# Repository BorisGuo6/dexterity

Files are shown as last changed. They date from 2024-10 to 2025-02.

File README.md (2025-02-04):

# Project Dexterity

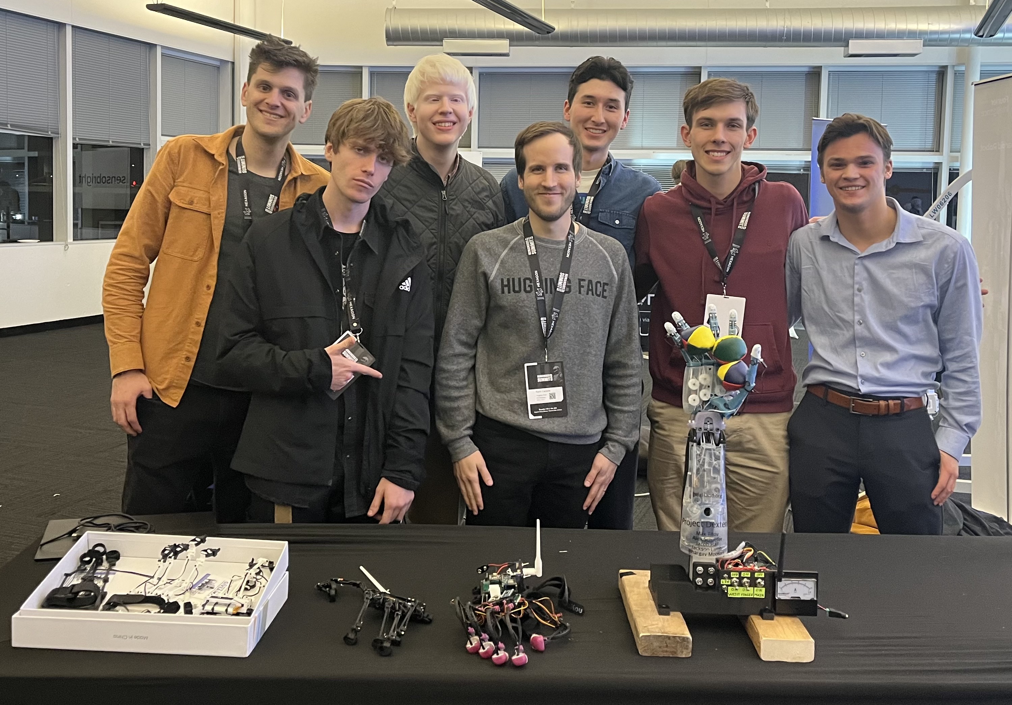
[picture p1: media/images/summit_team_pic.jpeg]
Team Pic at Humanoids Summmit


## Overview
Dexterity is a capstone project developed by ECE students at the University of Virginia (Class of 2025). The project consists of a robotic hand that can be controlled using a haptic feedback glove, providing a natural and intuitive way to control robotic movements while receiving tactile feedback. Three members of our team traveled to the Bay Area in December 2024 to showcase the project at the [Humanoids Summit](https://humanoidssummit.com/) in the Hugging Face booth (pictured above).

An summary of the project can be found in these [Figma slides](https://www.figma.com/deck/h1ZrgHnDu9oTQfUKUapgQW/Dexterity-Progress-Report?node-id=32-46&t=BGETurAAA480CFCk-1).

## Videos

The videos below showcase how the system's responsiveness and precision enable it to consistently catch balls.

https://github.com/user-attachments/assets/b5050c01-b495-40dd-bd65-899a9acaca80

https://github.com/user-attachments/assets/4d67e1bd-996e-49d0-b71a-232bf0a58b3a

## Project Structure
### [Firmware](firmware/)
- `HapticGlove/` - Firmware for the V2 control glove
- `RoboticArm/` - Firmware for the dexhand
- `PrototypeGlove/` - Firmware for the prototype control glove 
- `ESPNOW/` - ESP-NOW wireless communication implementations
- `test/` - Various test implementations and debugging tools

### [Hardware](hardware/)
- `cad/` - CAD files for 3D printing
  - `arm base/` - CAD files for the arm base and wire organization
  - `glove v2.4/` - CAD files for the latest interation of the V2 glove
  - `old/` - CAD files for the previous iterations of the V2 glove
- `pcb/`
  - `Forearm/` - PCB design files for the forearm
  - `Hand/` - PCB design files for the hand
  - `Library/` - KiCad library files
  - `gerber/` - Gerber files for manufacturing

### [Capstone](capstone/)
- `requirements/` - Project requirements and specifications from our capstone class 
- `reports/` - Project reports and presentations from our capstone class 

### [Media](media/)
- `images/` - Photos of the project and components
- `videos/` - Demo videos and presentations
- `diagrams/` - System diagrams and illustrations

## Features

### Robotic Arm
- Based on the open-source [Dexhand](https://www.dexhand.org/) project
  - Forearm shell and arm base were FDM printed using PETG filament
  - Everything else was resin printed using ABS-like resin, which provided smoother finishes and more accurate fits due to the higher resolution of SLA printing
- 16 degrees of freedom (DOF) across five fingers
  - 3 DOF per finger (flexion of PIP, flexion of MCP, abduction/adduction)
  - 4 DOF for thumb (extra degree for rotation)
  - Controlled by EMAX ES3352 digital servos
- 2 DOF in the wrist (pitch and yaw)
  - Controlled by Feetech SCS2332 serial servos 
  - These provide increased range of motion and torque in addition to having overcurrent protection
- Controlled by ESP32-S3 DevKitC-1 microcontroller
  - Housed on a Proto-PCB
  - ESP-NOW protocol for low-latency communication
- Force-sensitive resistors on each fingertip
  - 5kg maximum pressure sensing
  - These are wired up to a voltage divider circuit that connects to ADC channels on the ESP32
- System is powered by a 6V 10A power supply
  - Directly supplies power to servos
  - 3.3V regulation for control electronics
  - Wired through an amp meter for monitoring current draw

<p float="left">
  
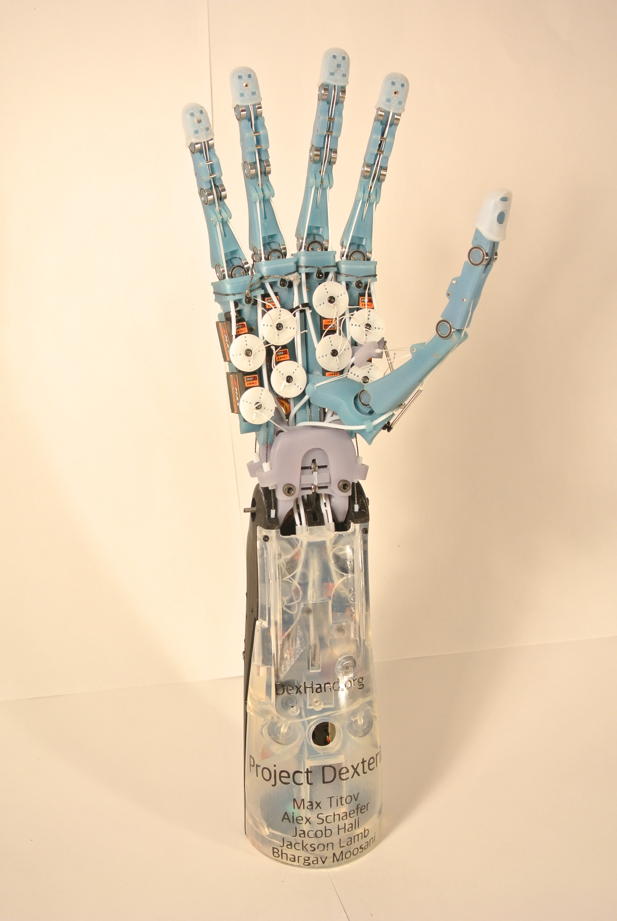
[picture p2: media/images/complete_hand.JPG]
   
</p>

### Prototype Glove
- Original repository can be found here: [Prototype Finger Tracker](https://github.com/max-titov/finger-tracker)
- Hall effect sensor-based finger tracking
  - Each joint that was tracked had a rotating magnet and a hall effect sensor
  - 3 DOF per finger (flexion of PIP, flexion of MCP, abduction/adduction)
  - 4 DOF for thumb (extra degree for rotation)
  - Multiplexed sensor reading
- Controlled by a Xiao ESP32-C3 microcontroller
  - ESP-NOW protocol for low-latency communication
- Provided very accurate and responsive finger tracking

<p float="left">
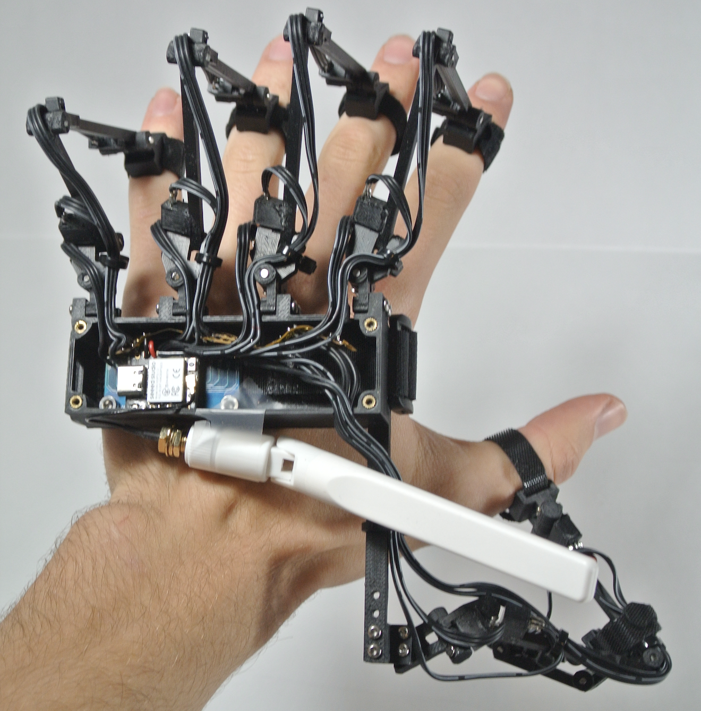
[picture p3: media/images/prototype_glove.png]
  
</p>

### V2 Control Glove
- Same hall effect sensor-based finger tracking as the prototype glove
  - 16 sensors total
  - Electrical complexity of the system introduced a lot of noise into the system, making the finger tracking less accurate than the prototype glove
- Dual PCB design
  - Hand PCB for sensors and haptics
  - Forearm PCB for processing and power
  - Connected with two ribbon cables
- Dual IMU system for wrist orientation
  - One IMU on hand PCB
  - One IMU on forearm PCB
  - Quaternion-based orientation calculation
- Haptic feedback system
  - Linear Resonant Actuators on each fingertip
  - I2C multiplexer for managing multiple LRA drivers
  - Variable intensity based on pressure sensing
- 3D printed design
  - Finger buckets housed LRA drivers and clamped onto fingers using rubber bands
  - Modular finger assemblies allowed easy swapping of parts during development
  - 2 straps per PCB housing attached the device to your hand
- Controlled by ESP32-S3 DevKitC-1 microcontroller
  - Housed on the Forearm PCB
  - ESP-NOW protocol for low-latency communication
- Control panel with LED indicators and mode switches
- Capable of running on battery power due to the onboard 3.3V regulator

<p float="left">
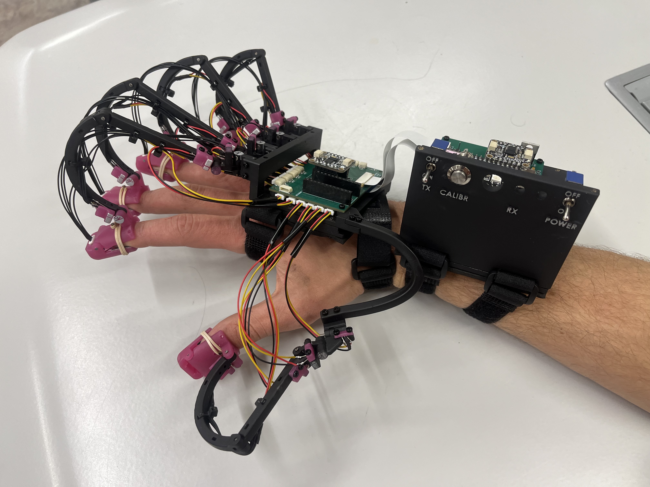
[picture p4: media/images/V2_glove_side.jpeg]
  
</p>

## Getting Started
1. Good luck with building everything :)
2. Clone the repository
3. Install PlatformIO extension for VSCode
4. Open the desired project folder
5. Build and upload to your device

## Authors

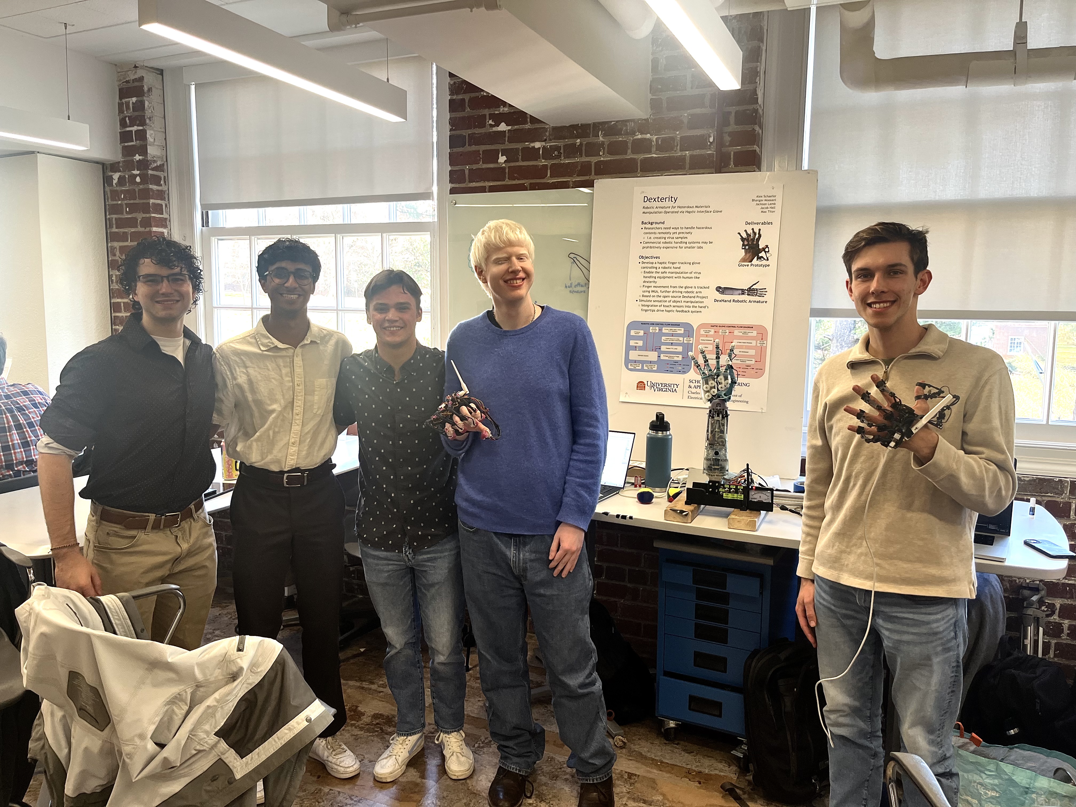
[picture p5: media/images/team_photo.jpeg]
Team Pic at UVA Demo Day


- Max Titov 
  - Led the team by doing high level design of the whole system, assembled the robotic arm, designed the control gloves, and developed finger tracking/control libraries
  -   
- Alex Schaefer 
  - Architected the embedded software system, implemented ESP-NOW communication, and developed the high-level control structure using multi-threading
  -  
- Jackson Lamb 
  - Designed and tested the dual PCB system for the control glove and developed libraries for the control panel interfaces
  -  
- Jacob Hall 
  - Implemented the dual IMU system for wrist tracking, including quaternion mathematics and calibration routines
  -  
- Bhargav Moosani 
  - Designed and implemented the haptic feedback system using LRAs and force sensors, including wireless integration
  -  

## Acknowledgments
- [Original Dexhand Repository](https://github.com/TheRobotStudio/V1.0-Dexhand/) - Our robotic hand design is based on The Robot Studio's Dexhand project, licensed under CC BY-NC-SA 4.0.
- [Dexhand Website](https://www.dexhand.org/) - Trent Shumay from IoT Design Shop built two Dexhands and put together a website that compiled info about the project into a single page.
- [Prototype Finger Tracker](https://github.com/max-titov/finger-tracker) - My first glove that tracked 16 DOF of the fingers. This glove was used in a lot of the demonstrations of the teleop due to its better finger tracking capabilities.
- [Nepyope's Youtube](https://www.youtube.com/watch?v=iPtgvh6fNdQ) - The video of the first 16 DOF glove using hall effect sensors that inspired this whole project.
- [Nepyope's Project Homunculus](https://github.com/nepyope/Project-Homunculus) - The repository for the glove that inspired this project.

## License
This project is licensed under the MIT License - see the LICENSE file for details

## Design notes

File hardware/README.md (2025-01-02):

# Hardware

This directory contains the hardware design files for the project, organized into three main sections:

## BOM (Bill of Materials)
The Project Dexterity BOM excel spreadsheet (also available as a [google sheet](https://docs.google.com/spreadsheets/d/1TfbwuFHU-D9O60yxQ3oRrJCOd3qs4ftfMmc7sZDtarE/edit?usp=sharing)) contains part lists organized into 3 sheets: 
- Robotic Arm BOM
- Control Glove BOM
- General BOM

## CAD (Computer-Aided Design)
The CAD directory contains 3D models and mechanical design files for the physical components of the project. The models were designed in SolidWorks and are avaiable as SLDPRT files. Each folder contains a folder with all the STLs as well.
- `arm base/` - CAD files for the arm base and wire organization
- `glove v2.4/` - CAD files for the latest interation of the V2 glove
- `old/` - CAD files for the previous iterations of the V2 glove

## PCB (Printed Circuit Board)
The PCB directory contains the electronic design files for the circuit boards. These include:
- `Forearm/` - PCB design files for the forearm
- `Hand/` - PCB design files for the hand
- `Library/` - KiCad library files
- `gerber/` - Gerber files for manufacturing

We ordered the PCBs from [JLCPCB](https://jlcpcb.com/). Pictures of the PCBs are below:

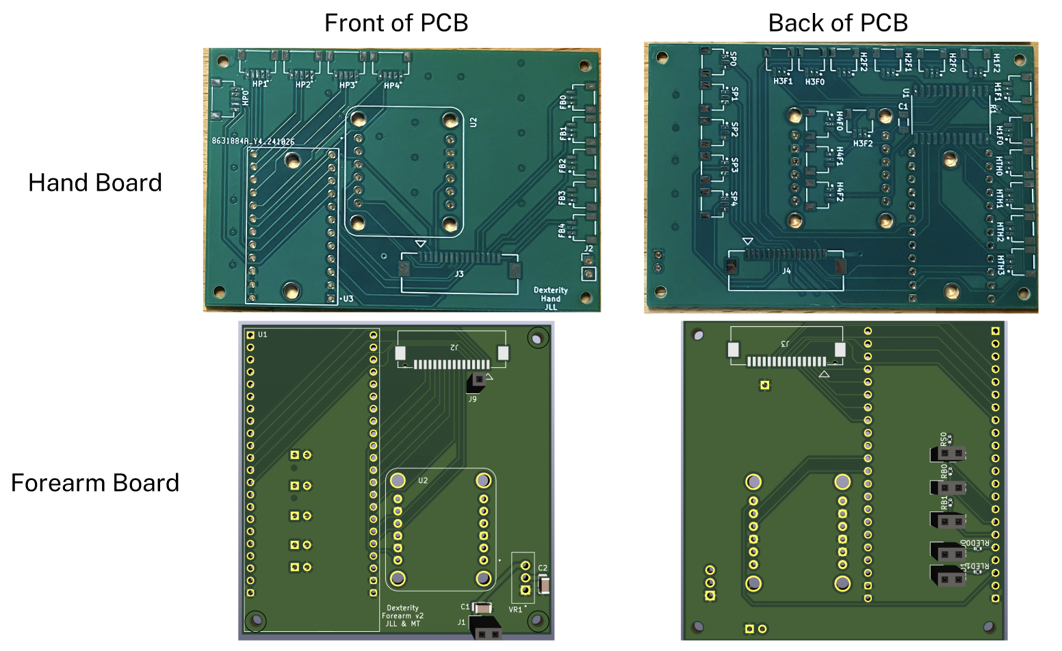
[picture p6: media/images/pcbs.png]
PCBs


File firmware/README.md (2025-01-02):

# Firmware

The Dexterity system consists of a haptic control glove and robotic arm that work together to enable remote manipulation of objects. The system uses ESP-NOW wireless communication to transmit position and force feedback data between the glove and arm with low latency.

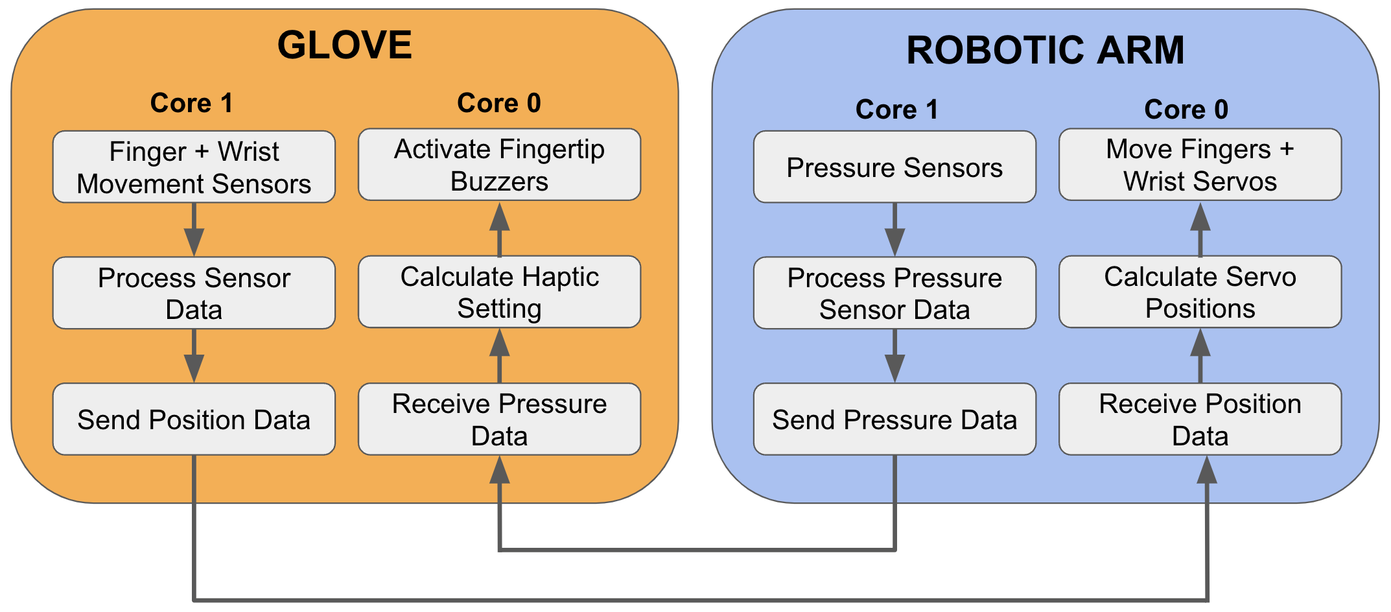
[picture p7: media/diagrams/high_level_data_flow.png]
High Level Data Flow Diagram


## System Architecture

The ESP32's dual-core architecture enables parallel processing of haptic feedback and position control. Core 1 handles initialization, with FreeRTOS managing resource allocation across both cores. The pressure sensor-to-LRA feedback pipeline runs on one core, while position sensing-to-servo control runs on the other. Timer-based ISRs ensure 50 Hz processing rates for both pipelines. The system uses ESP-NOW for wireless communication, with pressure data categorized into five intensity levels for haptic feedback, and position data from Hall Effect sensors and IMUs controlling servo movements.

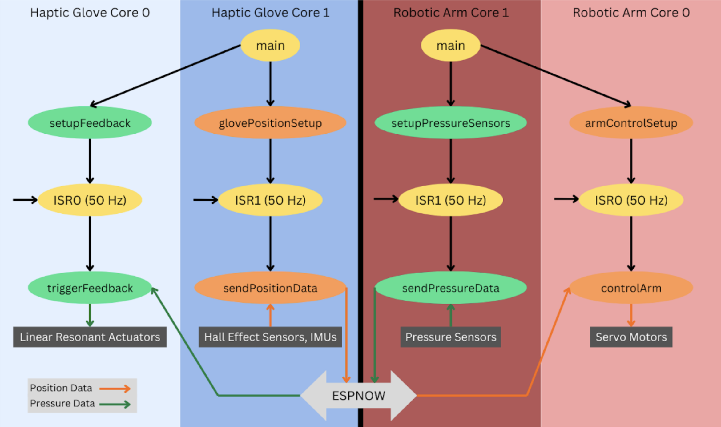
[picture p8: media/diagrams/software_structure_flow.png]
Software Data Flow Diagram


## HapticGlove
Firmware for the V2 control glove. The glove uses hall-effect sensors and IMUs to track finger and wrist movements, which are processed and sent wirelessly to control the robotic arm. It receives pressure sensor data from the arm and provides haptic feedback through LRA vibration motors on the fingertips. Descriptions of each library can be found here: [HapticGlove Libraries](HapticGlove/lib/)

## RoboticArm 
Firmware for the robotic hand. The arm receives position commands from the glove and moves its servos to match the user's movements. It uses pressure sensors to detect contact forces and sends this data back to drive the glove's haptic feedback. Descriptions of each library can be found here: [RoboticArm Libraries](RoboticArm/lib/)

## PrototypeGlove
Firmware for the initial prototype control glove used for testing and development. Descriptions of each library can be found here: [PrototypeGlove Libraries](PrototypeGlove/lib/)

## ESPNOW
Example implementations and testing code for ESP-NOW wireless communication between devices.

## test
Various test implementations and debugging tools for development and validation.

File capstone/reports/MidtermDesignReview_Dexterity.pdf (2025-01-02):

## Dexterity - Midterm Design Review

Alex Schaefer
Bhargav Moosani
Jackson Lamb
Jacob Hall
Max Titov

## Dexterity: Overview

Background

- Researchers handle hazardous contents in labs frequently → risky predicament
- i.e. preparing virus samples or handling poisonous substances
- Robotic handling systems are expensive
- Barriers of entry for smaller labs

Objectives

- Provide researchers and labs with a safe, cost-effective approach to hazardous material manipulation, which can be used for their lab-specific needs

## Dexterity: Deliverables

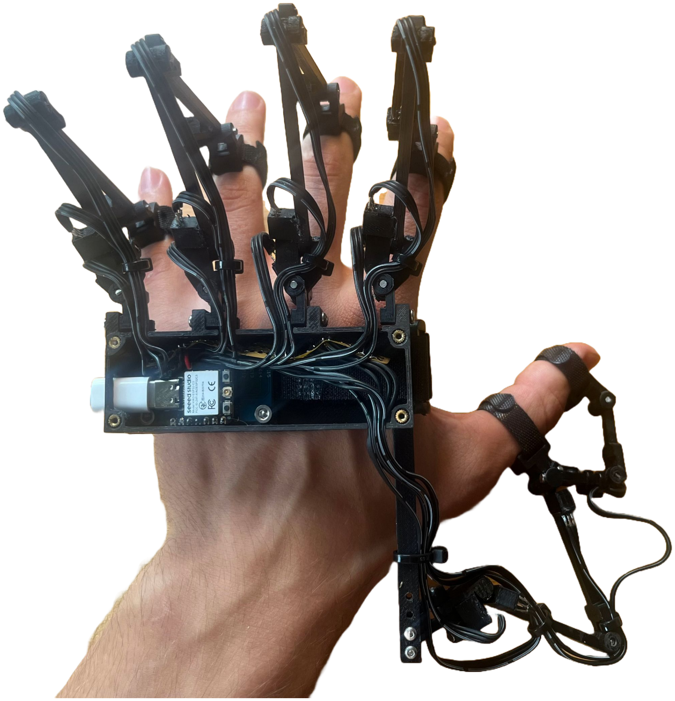
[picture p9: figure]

Control Glove Prototype

Control Glove

- Hall effect sensors and IMUs track hand motion to drive the robotic armature
- Linear actuators provide haptic pulses for touch feedback from the robotic arm

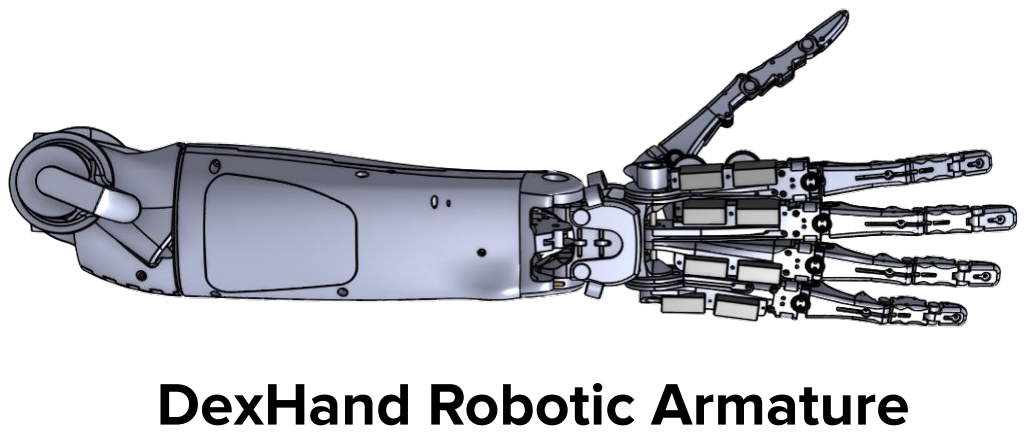
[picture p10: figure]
DexHand Robotic Armature

Robotic Armature

- CAD based off the open-source Dexhand project
- Pressure sensors on each fingertip to drive linear actuators on control glove

# Design

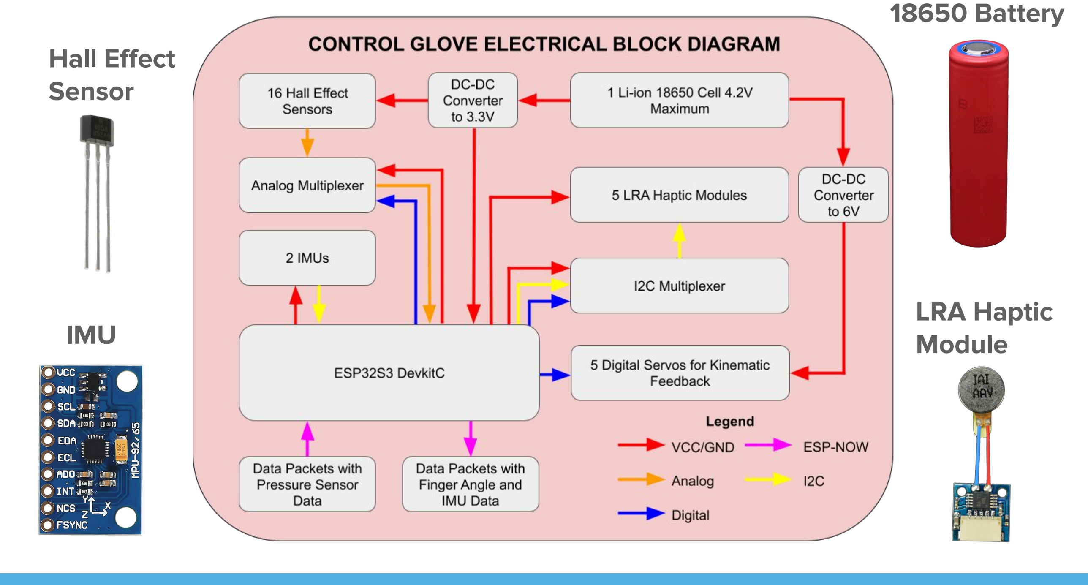
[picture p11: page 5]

Hall Effect
Sensor

IMU

LRA Haptic
Module

18650 Battery

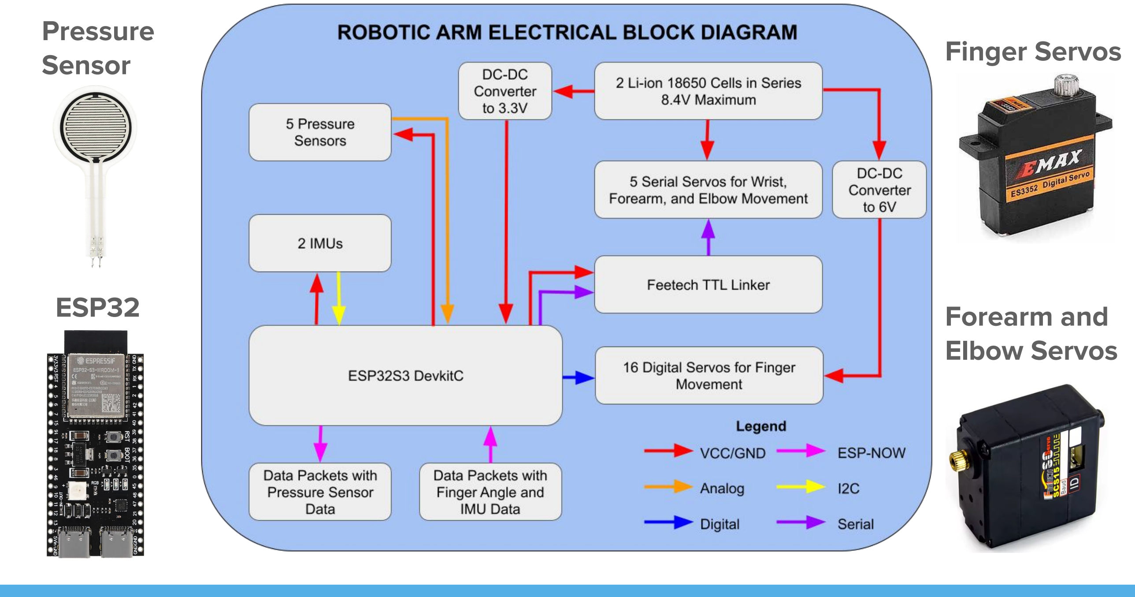
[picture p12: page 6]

Pressure
Sensor

ESP32

Finger Servos

Forearm and
Elbow Servos

## Glove Sensor Processing Software Flowchart

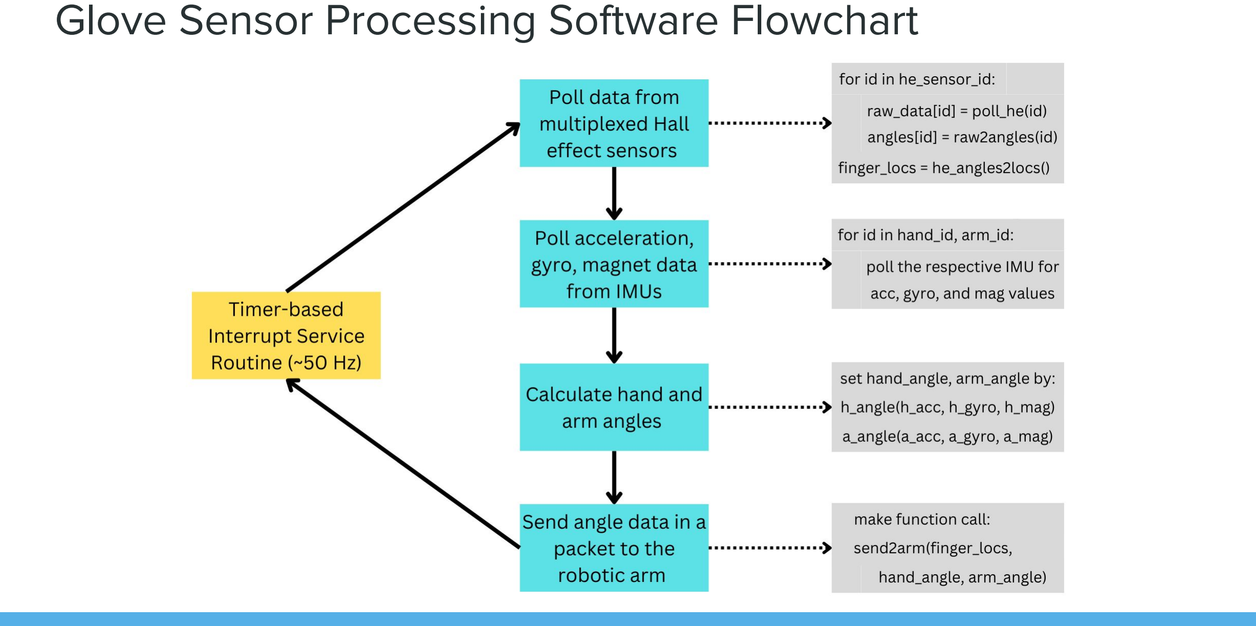
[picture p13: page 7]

## Glove Haptic Data Processing + Control Software

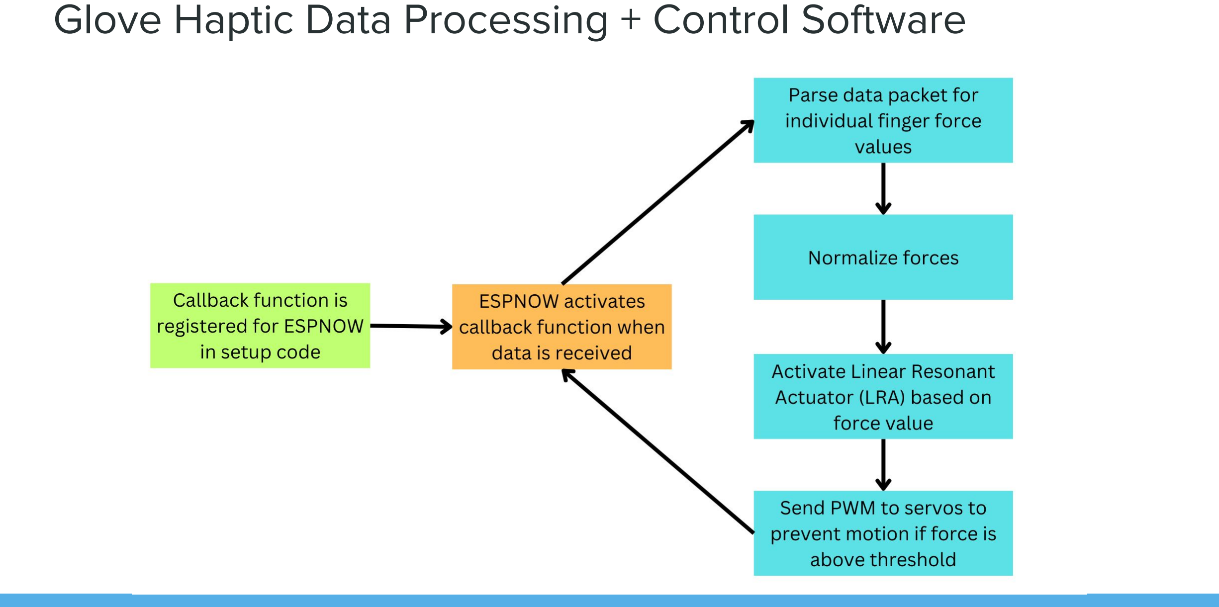
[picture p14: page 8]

ESPNOW Wireless Communication Protocol

Callback Function ran every time a packet from robotic arm is received

- Packet parsed into individual finger forces (from touch sensors)
- Forces are normalized
- Normalized forces are used to activite LRAs (Linear Resonant Actuator)
- (Optional) Servo Motors on Glove actuated to prevent motion

## Robotic Arm Software

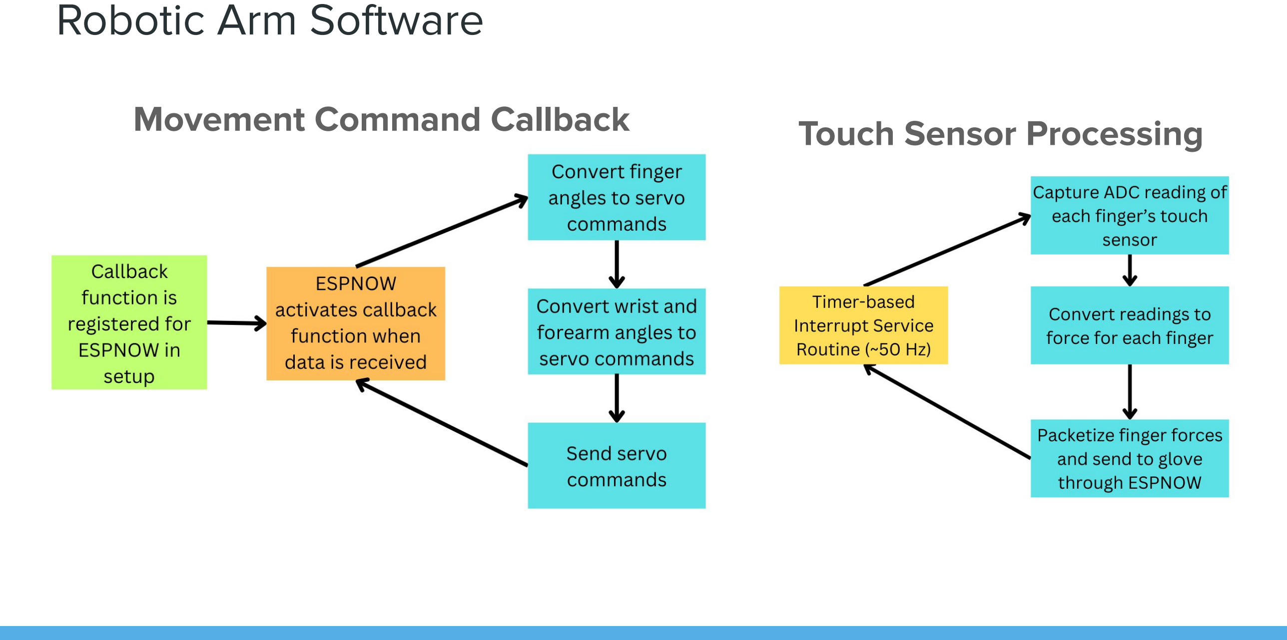
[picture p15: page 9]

Movement Command Callback | Touch Sensor Processing

## Control

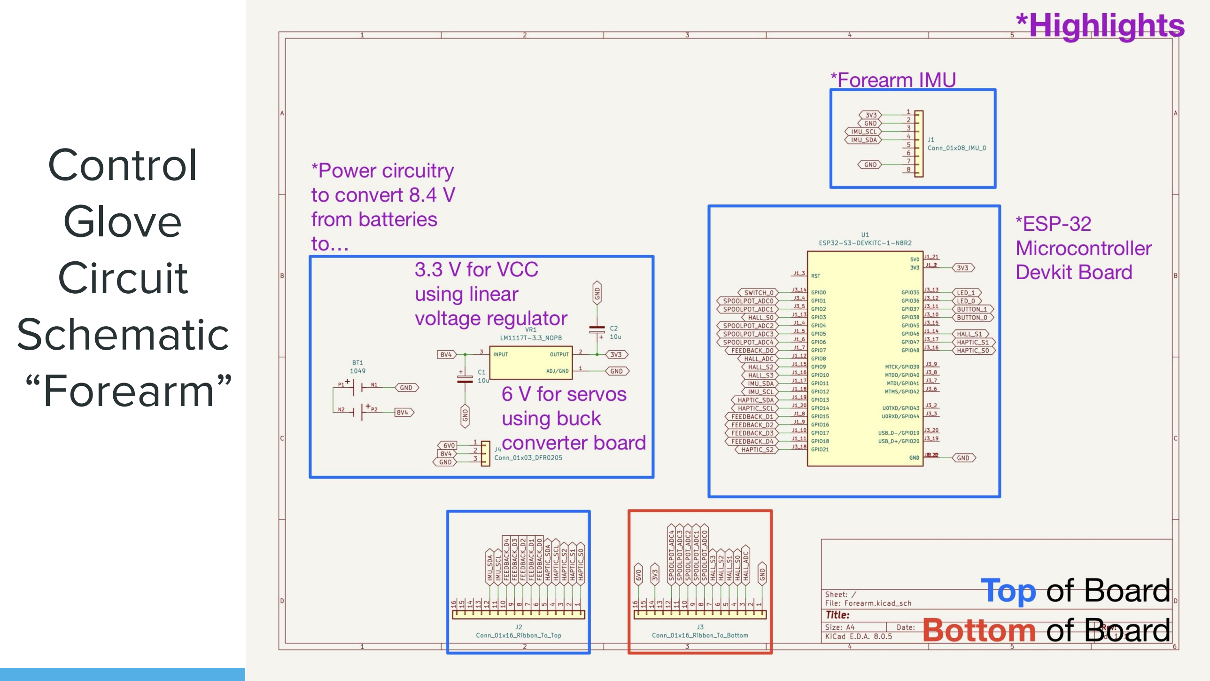
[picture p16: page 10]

## Glove Circuit Schematic “Forearm”

## Control

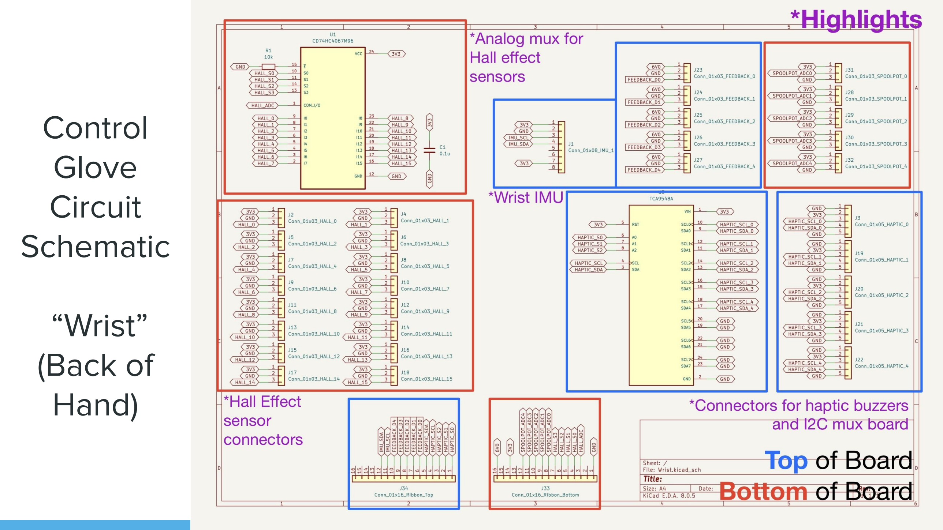
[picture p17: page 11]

## Glove Circuit Schematic

## “Wrist” (Back of Hand)

# Test Plan

## Robotic Arm Testing

After assembling the finger and thumb assemblies:

- Test 3 Degrees of Freedom (DOF) for each finger to ensure each joint can move independently and with the correct range of motion.
- Test 4 DOF for the thumb to confirm full movement, including opposability.

After assembling the wrist and forearm:

- Test 2 Degrees of Freedom for wrist
- Test 2 Degrees of Freedom for forearm

## Control Glove Testing

### 1. Hall Effect Sensor

- Test the 16 hall effect sensors on a breadboard to ensure they are reading magnetic field changes accurately

### 2. Finger Linkage Assembly

- Test that the 16 hall effect sensors still work after assembly, ensuring no mechanical interference

### 3. IMU Accuracy

- Test both IMUs to verify that they provide accurate orientation data post-assembly

### 4. Communication

- Test sending and receiving packets between ESP32 microcontrollers to verify reliable wireless data exchange

## Complete System Testing

### 1. Communication

- Test that packets are successfully sent and received between both ESP32 microcontrollers in complete system

### 2. Control

- Test controlling 1 finger with the control glove
- Test controlling all 5 fingers with the control glove
- Test controlling wrist movement using IMU data
- Test controlling forearm and elbow movement using IMU data

### 3. Haptic Feedback

- Test the haptic response of all 5 fingers to confirm uniform and reliable feedback across all fingers

### 4. Calibration

- Test the calibration of the control glove to the robotic arm to ensure that hand movements and forces are accurately translated to the robotic system

# Timeline

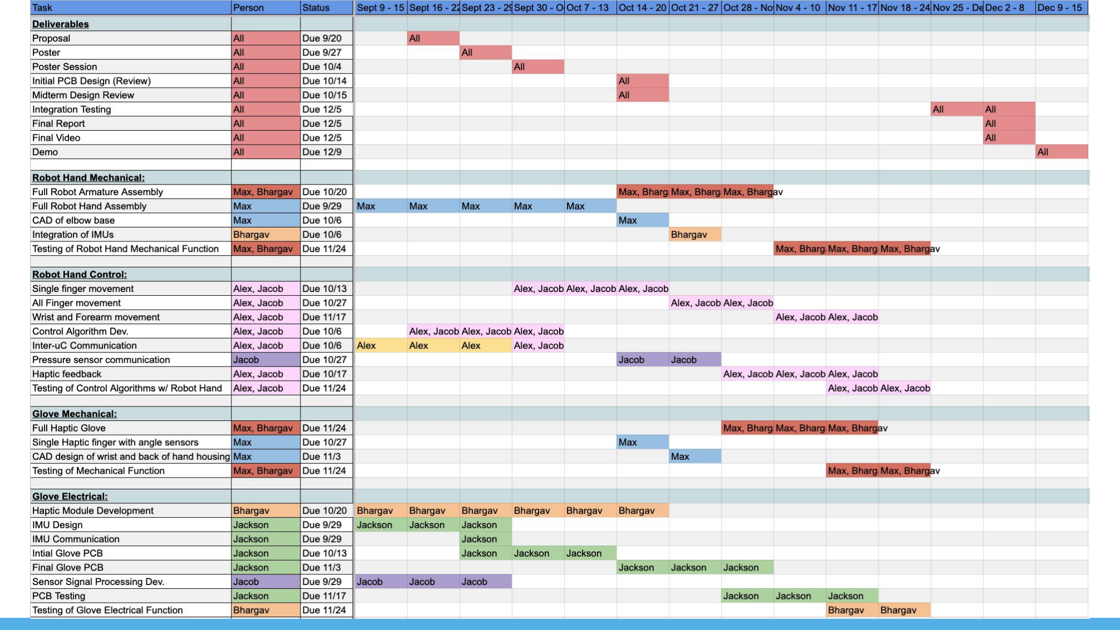
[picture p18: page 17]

# Questions?

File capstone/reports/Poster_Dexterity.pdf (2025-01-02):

# Dexterity

### Background

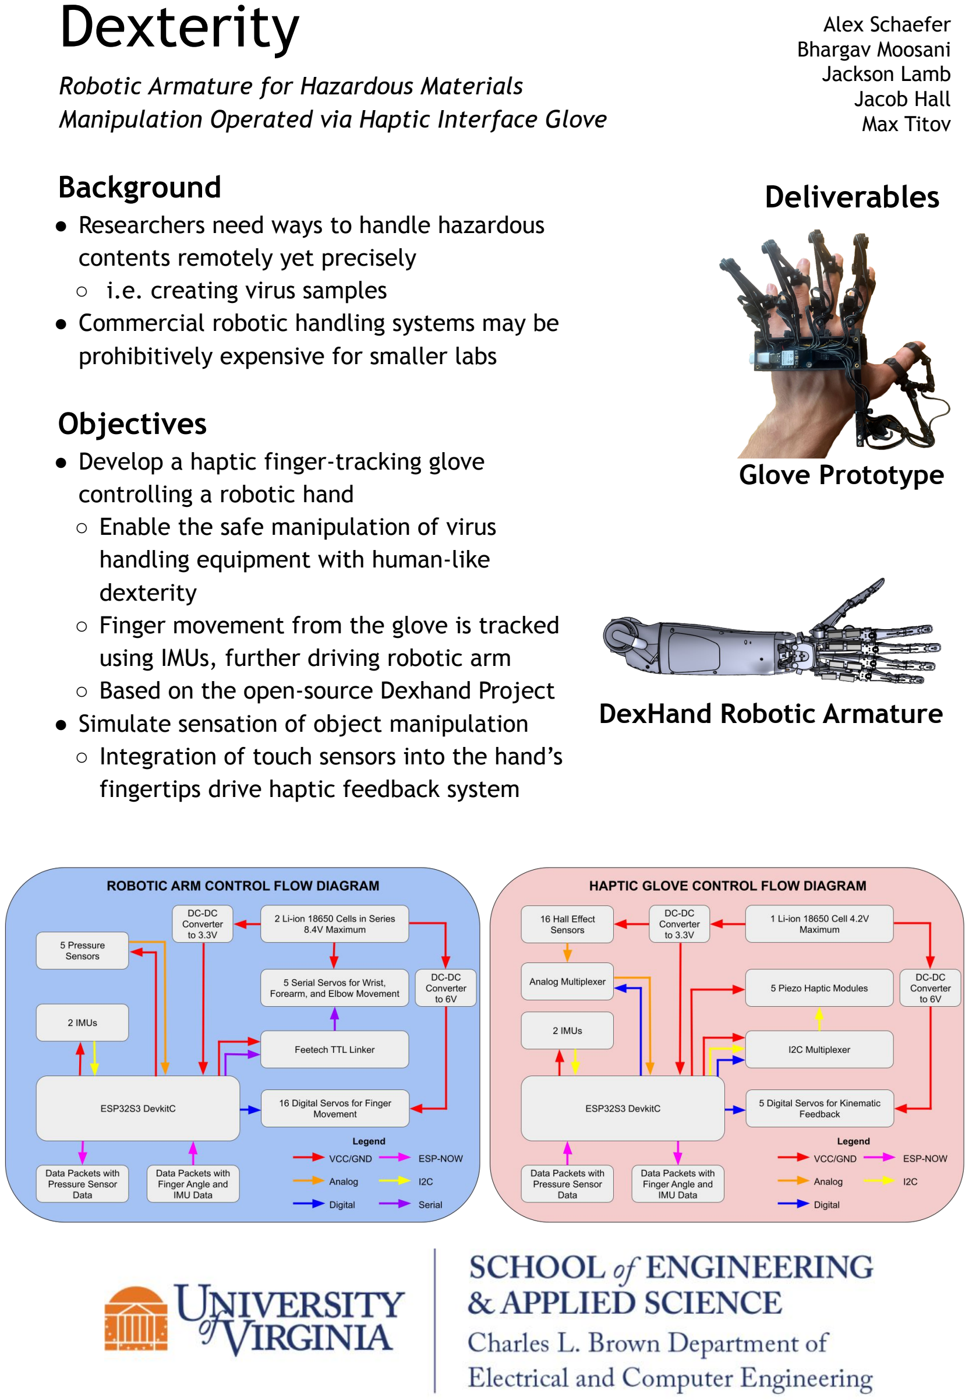
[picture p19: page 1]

Robotic Armature for Hazardous Materials Manipulation Operated via Haptic Interface Glove

- Researchers need ways to handle hazardous contents remotely yet precisely
- i.e. creating virus samples
- Commercial robotic handling systems may be prohibitively expensive for smaller labs

### Objectives

- Develop a haptic finger-tracking glove controlling a robotic hand
- Enable the safe manipulation of virus handling equipment with human-like dexterity
- Finger movement from the glove is tracked using IMUs, further driving robotic arm
- Based on the open-source Dexhand Project
- Simulate sensation of object manipulation
- Integration of touch sensors into the hand’s fingertips drive haptic feedback system

Alex Schaefer
Bhargav Moosani
Jackson Lamb
Jacob Hall
Max Titov

Glove Prototype

DexHand Robotic Armature

### Deliverables

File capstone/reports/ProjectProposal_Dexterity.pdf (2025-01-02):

# Dexterity

Robotic Armature for Hazardous Materials Manipulation Operated via Haptic Interface Glove Alex Schaefer, Bhargav Moosani, Jackson Lamb, Jacob Hall, Max Titov

Abstract

This project aims to develop a haptic finger-tracking glove that controls a robotic hand, enabling safe manipulation of hazardous materials while maintaining human-like dexterity. The system consists of a glove that tracks the user’s finger movement, coupled with inertial measurement units (IMUs) to monitor hand and forearm orientation. This motion-tracking system drives a robotic arm based on the open-source Dexhand project. We will integrate touch sensors on each robotic fingertip that activate the glove's electromagnetic brake system. These brakes create tactile feedback by restricting finger movement, simulating the sensation of object manipulation. This haptic feedback, combined with the precise motion tracking, allows for intuitive and accurate control of the robotic hand in hazardous environments.

Background

The increasing need for safe and cost-effective solutions in laboratories handling hazardous materials has driven our team to develop a haptic finger and forearm-tracking glove system that controls a robotic hand. This system is designed to enable researchers to interact with toxic substances while maintaining human-like dexterity and without the need for expensive fume hoods or overly complex robotic setups. The core innovation of our project lies in creating a much more affordable and user-friendly alternative compared to existing commercial solutions, making this technology accessible to a wider audience of researchers and laboratories.

Prior Work

Commercial products such as HaptX [1], (https://www.zotero.org/google-docs/?hcelSB) SenseGlove [2], (https://www.zotero.org/google-docs/?vWltXo) and Weart [3] (https://www.zotero.org/google-docs/?kayynv) have set the standard in the haptic feedback and remote manipulation market, offering highly immersive and precise systems. These technologies allow users to interact with virtual environments or robotic systems while experiencing realistic tactile feedback. However, these products are often prohibitively expensive and primarily serve industrial applications, limiting their accessibility to smaller research labs and educational institutions.

In the open-source space, projects like LucasVR [4] (https://www.zotero.org/google-docs/?fwQZJJ) and Nepyope's VR Glove [5] (https://www.zotero.org/google-docs/?h1ueZ5) have demonstrated innovative solutions for hand-tracking and haptic feedback. These projects offer promising foundations, especially in terms of making the technology more accessible. However, they lack the focus on safe, real-world interaction with hazardous materials, as their primary use cases lie within virtual reality environments.

Our project differentiates itself in two key ways: cost and target audience. By leveraging open-source designs and affordable components, we aim to drastically reduce the overall cost of the system, making it viable for smaller research institutions and universities. Our system also targets laboratories that require safe manipulation of hazardous materials. Unlike existing virtual reality or industrial solutions, our glove allows researchers to remotely control a robotic hand to handle toxic substances with haptic feedback, improving both safety and ease of use without the need for costly equipment or infrastructure.

Coursework Preparation

Our coursework at the University of Virginia has provided a strong foundation for this project. Several key courses have directly prepared us for the technical challenges involved:

- Intro to Embedded Computing Systems has given us a solid understanding of microcontrollers and real-time systems, both critical for the responsive control of the glove and robotic arm.
- Electromagnetic Fields helped us understand the fundamentals of how electromagnetic braking systems can be implemented to simulate tactile feedback in the glove.
- Intro to Control Systems and Signals & Systems laid the groundwork for developing the precise control algorithms necessary for converting user hand movements into corresponding robotic arm movements.
- Electronics provided us with the skills to design and integrate the necessary hardware components, such as sensors and actuators, into a compact and efficient system.
- Computer-Aided Design has allowed us to design and/or modify existing models of both the glove and robotic arm components in a way that is both ergonomic and easy to manufacture, ensuring that the final product is as user-friendly as it is functional.

By applying the principles and techniques we have learned in these courses, we are well-equipped to develop a system that not only tracks hand movements accurately but also provides real-time, tactile feedback to the user. This combination of coursework and innovative design will allow us to bring a cost-effective, high-functioning tool to laboratories where safety and precision are paramount.

Description of Project

How it Works/Technical Details

Overview
As can be seen in Figure 1 below, the Dexterity system consists of a user-worn glove consisting of a suite of sensors with a haptic interface and a robotic arm controlled by the glove. At a high level, there sensor signals from each of the fingers and the forearm are processed into movement commands sent to the robotic arm. Upon receiving these commands, the robotic arm fingers and forearm are manipulated to match that of the glove as close as possible. The robotic arm has a suite of touch sensors, whose data is processed into haptic commands sent back to the glove. The glove processes these haptic commands and restricts movement of the user’s fingers.

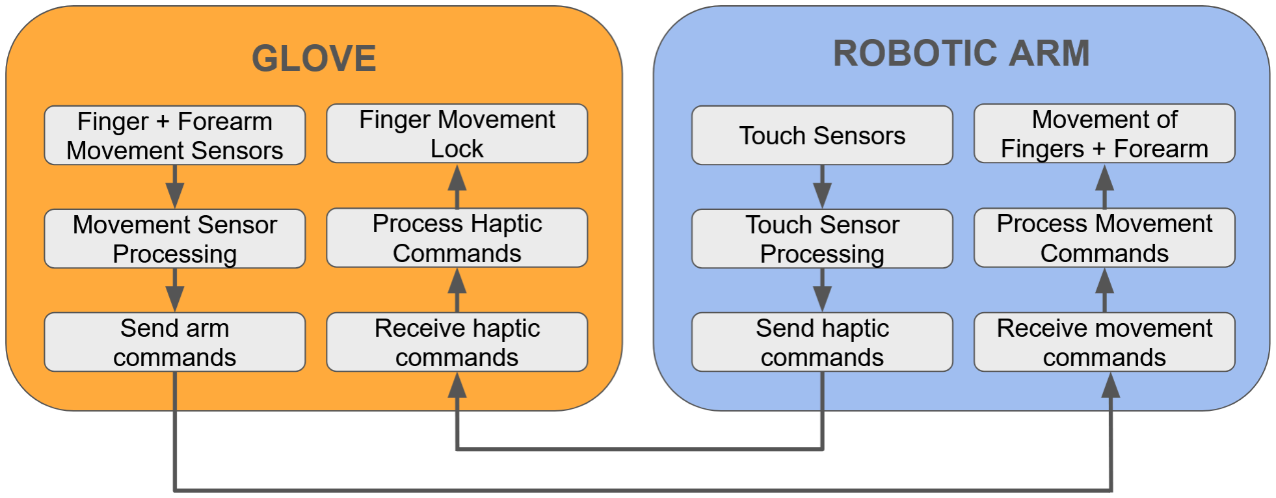
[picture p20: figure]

Figure 1: Complete System-Level Diagram

Robotic Arm
Our robotic arm is based on the open source project called the Dexhand [6]. (https://www.zotero.org/google-docs/?zinsQ2) The arm, up to the elbow, has 19 degrees of freedom that are controlled by servo motors. The fingers will account for 16 of these: 3 per finger and 4 for the thumb. The wrist has 2 degrees of freedom, and the rotation of the forearm accounts for the last degree of freedom. One modification we are making to the design is adding an elbow base with 2 degrees of freedom. This base will be securely attached to a table or rolling cart to provide stability to the rest of the hand. With our modifications, the hand will have a total of 21 degrees of freedom. An overview of the CAD can be seen in Figure 2.

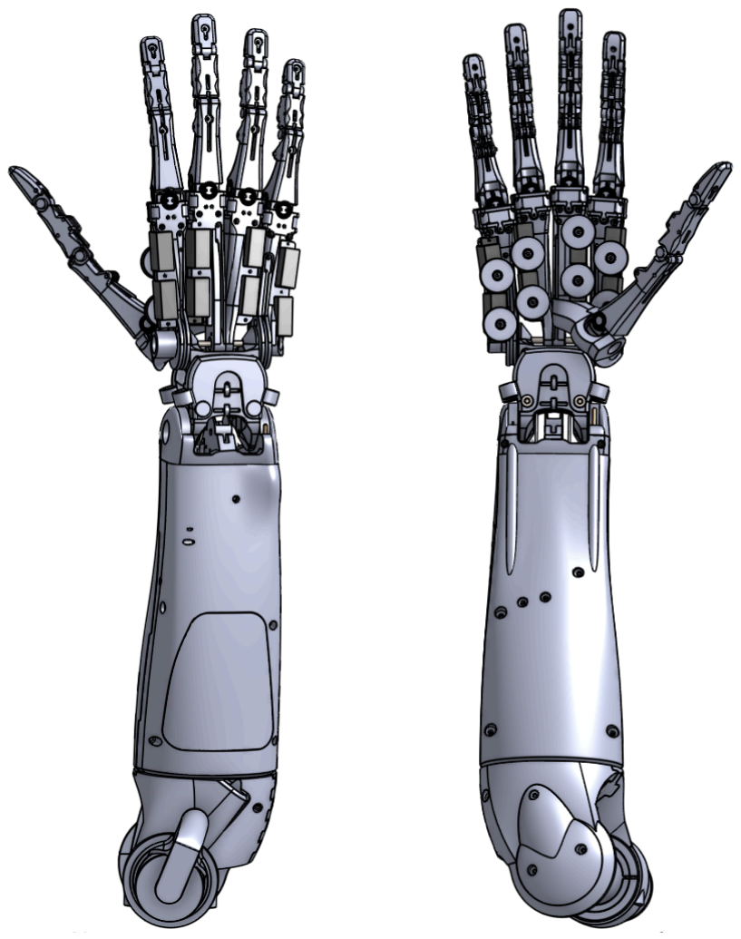
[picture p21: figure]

Figure 2: CAD Model of Robotic Arm

Another key modification that we are making to the original design is the integration of pressure sensors in each fingertip. These readings from the pressure sensors will be transmitted to the control glove to engage haptic feedback to create the sensation of holding an object in the user. Additionally we are adding two IMUs: one on the back of the robot hand and one on the back of the forearm. These sensors will be in the same locations on the control glove. To create wrist, forearm, and elbow movement, the robot hand will try to match its IMUs readings to the control gloves IMU readings by moving the wrist and forearm in the appropriate direction. This will be accomplished using PID (proportional integral derivative) [7] (https://www.zotero.org/google-docs/?FtU3I5) loops to control the servos.

This robotic arm control system is built around an ESP32S3 DevkitC microcontroller. It's powered by two Li-ion cells and uses DC-DC converters to regulate 6V for the digital servos and 3.3V for the ESP32. The control glove sends ESP-NOW [8] (https://www.zotero.org/google-docs/?ZmDn0H) data packets containing IMU and finger angle data. After processing this data, the ESP32 sends digital signals to control the 16 finger servos and serial data to control the 5 serial servos. The ESP32 will read the pressure sensor values using ADCs and send this data to the control glove using ESP-NOW. A diagram of this system is shown in Figure 3.

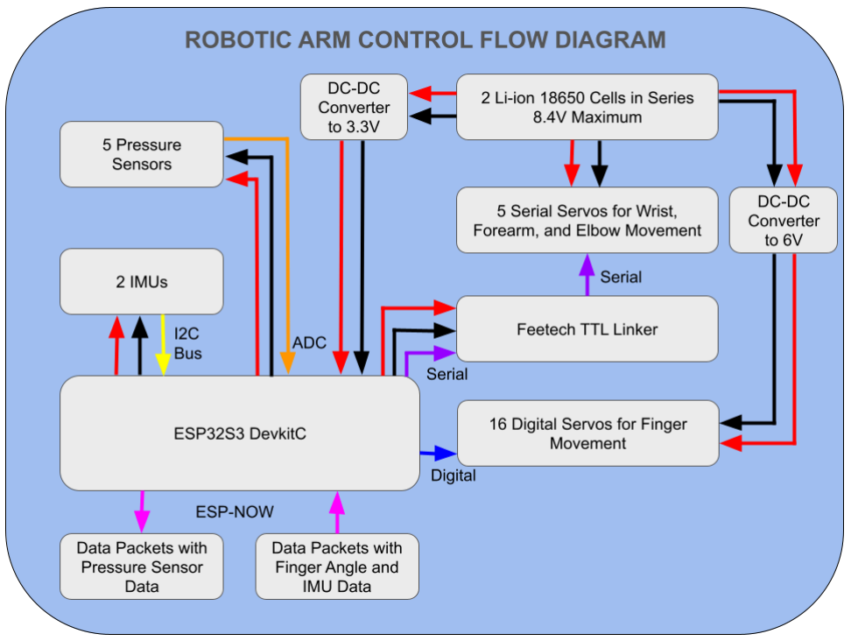
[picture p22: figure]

Figure 3: Robotic Arm Control Flow

Control Glove
For sensing motion of the user’s hand and forearm, the glove consists of 16 hall-effect sensors [9] (https://www.zotero.org/google-docs/?Ym5T6B) and two IMUs. Hall-effect sensors have an output voltage correlated with the strength of the magnetic field at its location. By positioning a small magnet near each of the hall-effect sensors such that the dipole of the magnet rotates as the joint is, we can capture an output voltage correlated with the degree to which that joint has moved. The IMUs are used to capture acceleration and angular velocity data from the wrist and forearm. There are also 4 electromagnetic brakes on the gloves that attach to lines connected to the top of the fingers. The microcontroller is placed on the forearm of the glove and connected to the IMU and power source via a drop-in PCB. A PCB on the back of the hand holds an IMU and a digital multiplexer. The two PCBs are connected via a ribbon cable, which has power, hall-effect sensor selection lines, data lines for the hall-effect sensors, two lines for communication with the IMU, and command lines for the electromagnetic brakes. Communication between the two IMUs and microcontroller will be mediated by I2C [10], (https://www.zotero.org/google-docs/?zNg5oo) a communications protocol with the advantage of requiring only two lines for communication between an arbitrary number of devices.

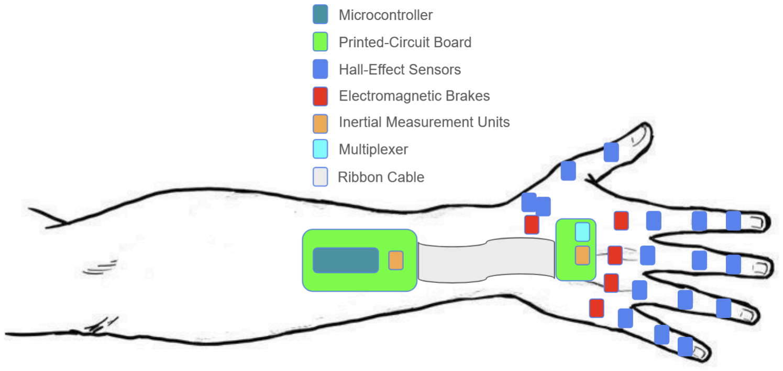
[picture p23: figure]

Figure 4: Control Glove Component Overlay

Each finger, not including the thumb, has 3 hall-effect sensors. These are used to measure the degree with which the finger is adducted, abducted, and flexed, which is demonstrated in Figure 5 below. For each finger, one sensor is placed just over the knuckle joint whose output voltage is highly correlated with the degree of abduction and abduction. The upper and lower joints on the fingers each have a sensor whose output is correlated with their degree of flexion. The digital multiplexor on the back of the hand is used to select which hall-effect sensor to read data from using minimal selection lines. To aid in visualization of this aspect of the glove, a glove prototype consisting only of the microcontroller in a small form factor, all hall-effect sensors, and the multiplexor is shown in Figure 6 below.

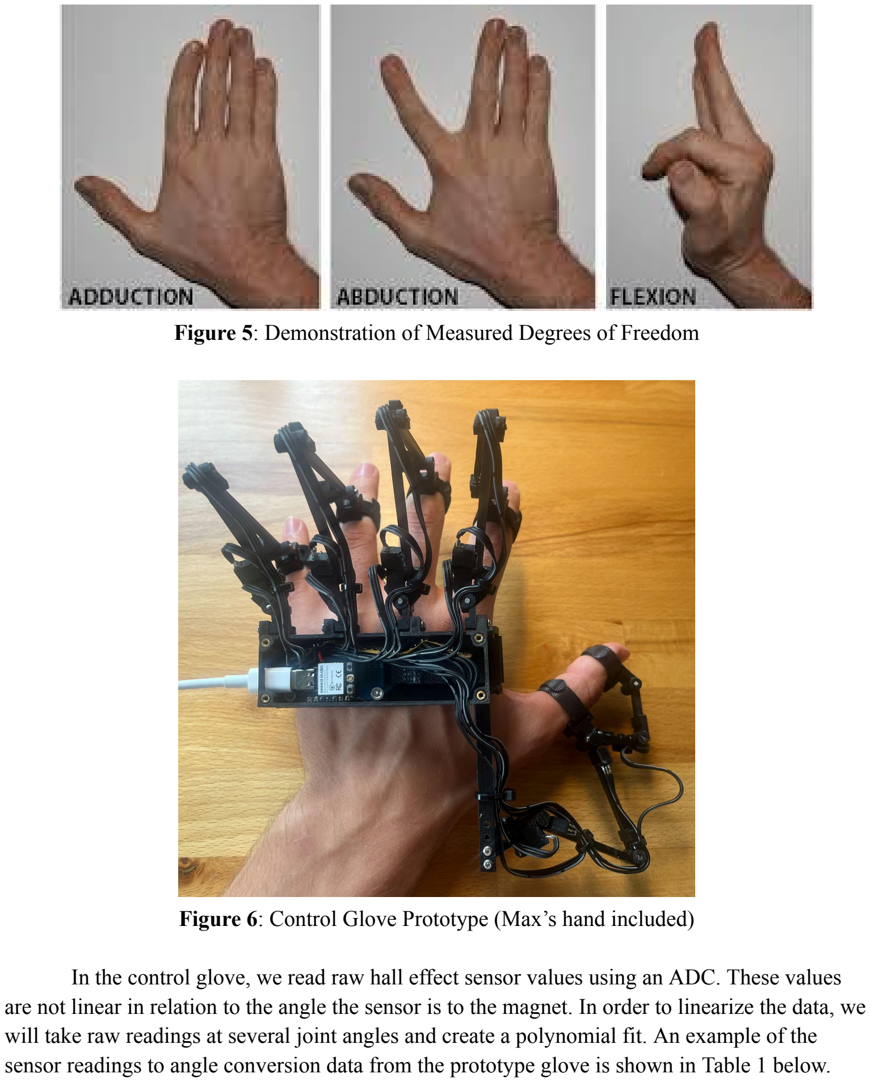
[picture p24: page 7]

Figure 5: Demonstration of Measured Degrees of Freedom

Figure 6: Control Glove Prototype (Max’s hand included)

In the control glove, we read raw hall effect sensor values using an ADC. These values are not linear in relation to the angle the sensor is to the magnet. In order to linearize the data, we will take raw readings at several joint angles and create a polynomial fit. An example of the sensor readings to angle conversion data from the prototype glove is shown in Table 1 below.

Table 1: Example Hall-Effect Sensor Readings to Angle Conversion Data
Raw Value | Angle of Joint
2040 | 30
2110 | 60
2220 | 90
2370 | 120
2500 | 150

Using a polynomial fit calculator, we created the following polynomial for a joint on the pinkie, where y is the angle of the joint and x is the raw value:

y =− 0. 000204869x

2
+ 1. 18023 − 1522. 07

After doing the above steps on all 16 joints, the control glove produces linearized data that corresponds to the actual angle of each joint. This can be seen in Figure 7.

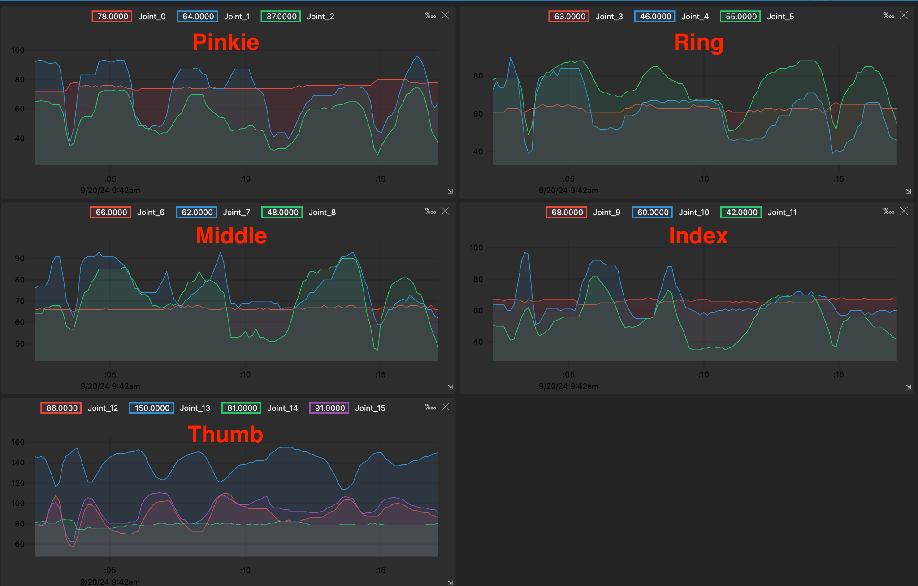
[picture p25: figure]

Figure 7: Finger Tracking Measurements via Hall Effect Sensor

The wrist and forearm both have an IMU that captures their acceleration and angular velocity in the X, Y, and Z directions defined by the unit itself, depicted in Figure 8 below. The MEMS (Micro-Electronic Mechanical Sensor) accelerometer output from the IMUs consist of the gravity vector no matter if the IMU is stationary or moving. Thus, because the IMU outputs the X, Y, and Z directional component of the gravity vector as the wrist and forearm rotates, we can back calculate the angle of rotation of the wrist and hand relative to that vector when the IMU is stationary or accelerating significantly slower than gravity. When the IMU is accelerating closer to the rate of gravity, then the acceleration and gyroscopic measurements can be used to calculate the angles of motion.

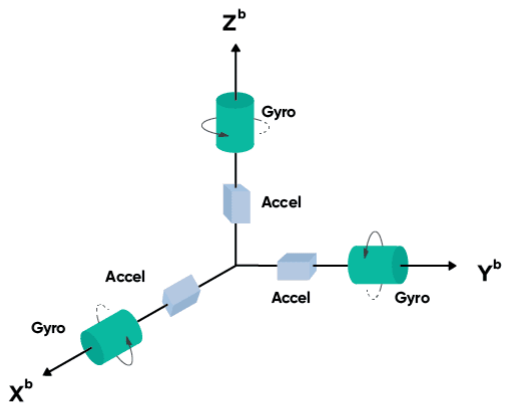
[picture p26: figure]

Figure 8: Wrist and Forearm Movement Axes

Each digit on the glove will have a haptic interface via an electromagnetic brake system. The brake system will lie at the base of each finger on the glove. When the robotic arm touches a physical object or obstruction, a current will be sent to the electromagnet to induce a magnetic field, causing the electromagnet to hit the braking surface. This will cause the tendon, in the form of a retractable nylon tether extending to the fingertips, to resist further extend, ultimately providing haptic feedback. The electromagnet components we will be using, developed by Adafruit Industries LLC [11], (https://www.zotero.org/google-docs/?QjHRel) have a 5V nominal voltage and draw 0.22 A at 5V, as well as 2.5 kg holding force.

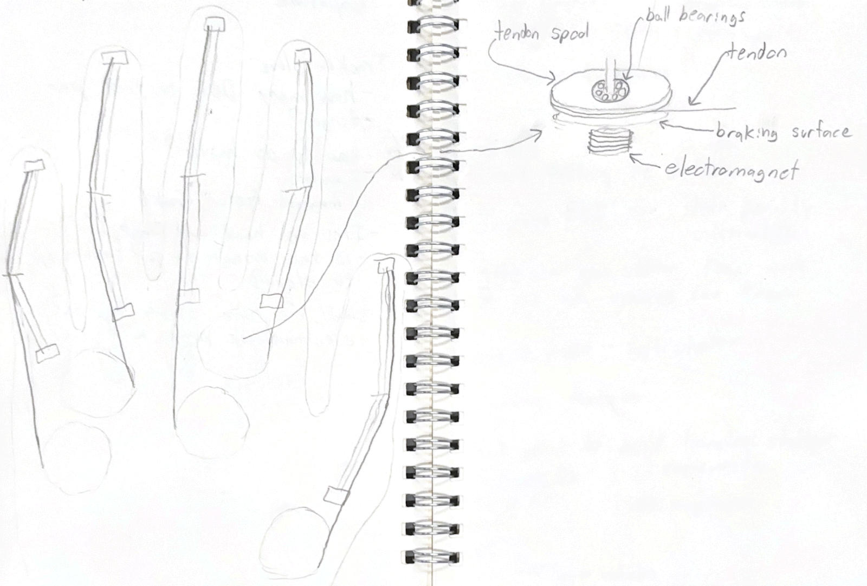
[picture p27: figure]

Figure 9: Initial Sketch of Haptic Brake System

Major Challenges
One of the major challenges associated with this project is the assembly of the robotic arm. Since the project group working on this has expertise in electrical and computer engineering, the mechanical aspects of the robotic arm will be a larger difficulty due to our smaller breadth of mechanical knowledge. Another major challenge is the design and calibration of the control systems between the robotic arm and the haptic glove. The group has some theoretical knowledge of control systems, but very limited application of this knowledge. Even with a well designed control system, the latency between the movement of the hand in the haptic glove and the robotic arm will be a limiting factor and a challenge. This is simply due to the difference in capabilities of the muscular systems in the human hand and the servo motors inside the robotic arm. It will be a challenge to identify how to implement an intuitive interface such that the robotic arm performs all of the important movements that the user’s arm makes, and it feels to the user like the robotic arm is mirroring the glove’s movements within a reasonable delay. An expected challenge is interference between the electromagnetics of the haptic interface and the Hall effect sensors. However, the group has planned for the event that the Hall effect sensors and electromagnets simply will not be able to operate within their necessary proximity, and a motor-driven braking system is reserved as a backup.

Applying standards mentioned in a later section will be another major challenge. While applying standards serves as an excellent guide for manufacturing a functioning and reliable product, ensuring that the standards are met can be rather difficult. The standards that we are applying relate to the integrity of our enclosures, electromagnetic compatibility, requirements of haptic interfaces, and minimizing robotic hazards.

Test Plan
This test plan outlines the systematic testing procedure for both the robotic hand and the control glove in our project. The tests will focus on the individual components, their integration, and the overall system functionality to ensure proper control and feedback.

Robotic Hand Test Plan

### 1. Servo Functionality Testing

- Before assembling any parts, test all the servos individually to verify they are fully operational:
- Full 180 or 360 degree rotation
- Stall torque within spec
- Speed of rotation within spec

### 2. Finger and Thumb Assembly Testing

- After assembling the finger and thumb assemblies:
- Test 3 Degrees of Freedom (DOF) for each finger to ensure each joint can move independently and with the correct range of motion.
- Test 4 DOF for the thumb to confirm full movement, including opposability.

### 3. Wrist and Forearm Assembly Testing

- After assembling the wrist and forearm:
- Test 2 DOF for the wrist (flexion/extension and radial/ulnar deviation) to ensure it moves smoothly and with precision.
- Test 1 DOF for the forearm (pronation/supination) to ensure proper control.

### 4. Elbow Base Assembly Testing

- After assembling the elbow base:
- Test 2 DOF for the elbow (flexion/extension and rotation) to confirm smooth movement and precise control.

### 5. Control Function Testing

- Test controlling 1 finger with the prototype glove to ensure accurate and responsive motion tracking.
- Test controlling all 5 fingers with the prototype glove to verify that all fingers can move independently and synchronously.
- Test all 5 pressure sensors on the robotic hand to ensure they provide accurate and consistent pressure data.
- Test both Inertial Measurement Units (IMUs) for accurate hand and forearm orientation data.

### 6. Communication Testing

- Test sending and receiving packets between two ESP32 microcontrollers to ensure reliable wireless communication.

Control Glove

### 1. Hall Effect Sensor Testing

- Test the 16 hall effect sensors on a breadboard to ensure they are reading magnetic field changes accurately.

### 2. Finger Linkage Assembly Testing

- After assembling the finger linkages with the hall effect sensors and rotating magnets:
- Test that the 16 hall effect sensors still work after assembly, ensuring no mechanical interference.

### 3. IMU Accuracy Testing

- Test both IMUs to verify that they provide accurate orientation data post-assembly.

### 4. Electromagnetic Brake Testing

- After assembling one electromagnetic brake:
- Test the brake with varying degrees of braking force to ensure it responds to control signals correctly.
- Test that the electromagnet does not cause interference with the hall effect sensor readings.
- After assembling all 5 electromagnetic brakes:
- Test that all brakes work with varying degrees of braking force to ensure uniform functionality.

- Test that the electromagnets do not cause interference with the hall effect sensor readings across all fingers.

### 5. Communication Testing

- Test sending and receiving packets between ESP32 microcontrollers to verify reliable wireless data exchange.

Complete System Testing

### 1. Communication Testing

- Test that packets are successfully sent and received between both ESP32 microcontrollers in the complete system.

### 2. Control Testing

- Test controlling 1 finger with the control glove to ensure smooth and accurate finger movement replication.
- Test controlling all 5 fingers with the control glove to confirm that all fingers respond accurately to glove movements.
- Test controlling wrist movement using IMU data to ensure smooth and precise wrist control.
- Test controlling forearm and elbow movement using IMU data to verify accurate orientation tracking and motion control.

### 3. Haptic Feedback Testing

- Test the haptic response of 1 finger to ensure the electromagnetic brake simulates tactile feedback accurately.
- Test the haptic response of all 5 fingers to confirm uniform and reliable feedback across all fingers.

### 4. Calibration Testing

- Test the calibration of the control glove to the robotic arm to ensure that hand movements and forces are accurately translated to the robotic system.

Physical Constraints

Because we are building upon the open-source Dexhand project, we already have a helpful guide for constructing the robotic hand assembly. This substantially reduces the difficulty of implementing the robotic hand, arguably the least familiar and most intimidating part of this project for us ECE majors. With this obstacle removed, our project faces only limited physical constraints.

Part Availability
The vast majority of the parts required for our project are either off-the-shelf components or 3D-printed. Our PCBs are the only exception to this general rule, but they can be readily ordered for manufacturing. Therefore, lack of part availability should not constrain our project.

Manufacturability
Beyond a healthy amount of troubleshooting, assembling our project once the parts have been gathered should be straightforward. However, each of the 3D-printed parts and PCBs will require on the order of hours and weeks, respectively. Although some of this time burden may be alleviated by printed parts or ordering PCBs for manufacture in parallel, we will need to carefully plan our manufacturing process to ensure that we obtain all required parts and leave time for remaking parts if necessary.

Cost Constraints
In the absence of external funding, our maximum budget is $1,000. This consists of $500 from the ECE department in addition to $100 from each of our five group members. At the time of writing, we do not anticipate and would rather avoid spending this maximum budget, but we are ultimately willing to do so if it is required to complete our project. Thus, cost should not constrain our project.
While this is true, the servo motors used to move the robotic hand are the single most expensive component of our project. Purchasing or eschewing servos supporting a wider range of motion for the hand would make the difference between staying within the department budget and dipping into our own pockets.

Resources and Equipment
Outside of the components we purchase, we will require a 3D printer to produce arts for our robotic hand assembly, a soldering iron for assembling our PCBs, and lab equipment such as an oscilloscope to test our circuits and communications between the hand and glove. All of this equipment may be accessed in the NI Lab. Additionally, one of our group members, Max Titov, has a personal 3D printer in his shop capable of producing the hand components from resin, so other teams using the 3D printers in the NI Lab should not be a significant concern for us.

Software Tools
We will use KiCad for circuit schematic and PCB design, Visual Studio Code coupled with the PlatformIO extension for embedded code development, and SolidWorks for any required computer-aided design work. All of these software tools are either freely available for all users or free for all of our group members by virtue of being students.

Comments on a Potential Production Version
A potential production version of our project would likely bear a strong similarity to the prototype because a major factor differentiating our project from similar products is its comparably low cost. Thus, the most salient physical constraints of a production version would result from increasing the scale of production rather than changing the device itself. Producing our prototype at a commercial scale could decrease costs in some respects but increase them in others. As an illustration, purchasing components in bulk would drive down the per-unit cost of production, but license fees may need to be paid for using certain software tools for a commercial rather than purely academic purpose. Additionally, we would need access to a larger 3D-printing capacity to produce a sufficiently large number of units.

Societal Impact

The relevant stakeholders in our project can be divided into two groups: potential users and those affected by said use. Potential users include scientists managing hazardous materials in a laboratory setting. They ostensibly aim to maximize safety for themselves, members of their team, and the public.
Entities affected by the project’s use may include the public at large, businesses, and governments. All these groups are generally concerned with the dangers posed by new technology, such as misuse and environmental impacts. The public at large wants to be safe from danger, businesses want to protect their employees, limit their liability, and maintain a good image, and governments strive to regulate technologies and protect their citizens.

Safety
Although our robotic arm promises to improve the safety of those handling hazardous materials, there is nonetheless a major safety concern worth considering: communication interruptions. These could arise intentionally or accidentally.
In the first case, a bad actor could intercept data between the glove and hand, convincing the latter that they are the glove. By doing so, the attacker could steal control of the hand from the user and issue actions ironically resulting in a safety hazard. For example, the attacker could trigger a premature or unwanted explosive reaction. Ideally, data transfer between the glove and hand would be mediated by a communication protocol featuring message encryption and signing.

Such a protocol would ensure that third parties could neither see the contents of messages nor forge messages from the glove.
In the second case, messages between the hand and glove could be corrupted by interference. This could cause the hand to act in unexpected ways, such as freezing in the middle of pouring a volatile chemical into a reaction mixture and producing an unstable solution. Sending a checksum along with each message and comparing each message against its associated checksum upon receipt would allow the glove and hand to detect and reject corrupted messages.
While communication interruptions are problematic, it should be noted that our robot arm is, by its very nature, intended to be operated over a distance sufficient to protect the user from the hazards posed by the materials being handled. For instance, a user handling explosives with our arm would be using it to avoid working within the blast radius anyway. Therefore, communication interruptions are likely as much of an issue of wasting materials or damaging property as they are of user safety.
A somewhat less acute safety concern is the force the glove applies to the user’s hand to provide haptic feedback. Care must be taken to ensure that such force is only as strong as it must be to provide feedback in order to prevent finger discomfort and injuries.

Unintended Uses
Despite our project’s intended use as a method for handling hazardous materials, we ultimately cannot control how our product is used once it ends up in customers’ hands. One concerning manner in which our product could be misused is the performance of medical or other procedures on humans and animals. Because we are not designing our robotic arm for the humane treatment of living things, injury could result from the device, for example, inadvertently applying too much force to a fragile limb.
Additionally, our project could conceivably be used to create hazardous materials for acts of terrorism instead of disposing of them. The robotic arm could empower bad actors to construct explosives, synthesize toxic chemicals, or extract bioweapons by making such activities safer. These misuses will likely draw attention from the public at large who will abhor or fear them as well as governments who, feeling pressure from constituents, seek to regulate them. Hazardous materials whose creation was mediated by our robotic arm pose a national security threat for governments because such materials may be used to commit acts of terror.

Environmental Impact
Because our project largely uses off-the-shelf electrical components, its environmental impact is similar to other groups’ projects. However, our robotic arm distinctly relies upon a large number of 3D printed parts. The primary environmental concerns with these parts are waste and difficulty of recycling. Firstly, printing parts that cannot support themselves necessitates the printing of support structures, which will be discarded as waste once printing is complete.

Secondly, the plastics used for 3D-printed parts, such as ABS and SLA, may either be rarely recycled municipality or not recyclable at all [12]. (https://www.zotero.org/google-docs/?AZXQHP)

External Standards

There are several standards to consider when it comes to the haptic glove and robotic arm interface. To follow some general standards, all casings will follow a NEMA Type 1 [13] (https://www.zotero.org/google-docs/?TqKOjT) to protect internal components from external materials. Additionally, Electromagnetic emissions standards described in IEC61000-6-8 [14] (https://www.zotero.org/google-docs/?Pkf1st) will be met.
There are also some application-specific standards that need to be met. ISO 9241-940
[15] (https://www.zotero.org/google-docs/?ojZPGm) provides methods to establish benchmarks, establish requirements, and identify problems with haptic interfaces. This is important to confirm the usability of the haptic interface presented by the glove. ISO 10218-1 [16] (https://www.zotero.org/google-docs/?SPJs9b) lays out guidelines for safe design of industrial robots and requirements for protective measures to eliminate or greatly reduce hazards associated with the robots. This is important to prevent the robotic arm from introducing more hazardous conditions into the situations that it should be minimizing hazard by its design.
There are several standards that are met within the system that do not need to be discussed in this section, because the designers of sub-components have already ensured the satisfaction of relevant standards. For example, the ESP32 allows for data exchange through WiFi, and already has built-in compatibility with IEEE 802.11 standards for local area networks. Since we are simply using a tool that enforces this standard on its own, we do not need to worry about implementing these standards ourselves.

Deliverables

The final project deliverable will consist of two overall components: the robotic arm and the haptic glove. The haptic glove will consist of two PCBs - one on the hand and one on the forearm. These PCBs serve to house the IMUs and carry all signals along to the ESP32, which is housed on the forearm PCB. These PCBs will be housed in a NEMA Type 1 compliant enclosure. The ESP32 within the haptic glove and an ESP32 within the robotic arm will send movement commands and haptic commands, respectively, to one another through an existing wireless communication protocol that is already implemented for the ESP32s. The robotic arm ESP32 will process the movement commands and control the servo motors on the robotic arm to match the state of the haptic glove. Meanwhile, the haptic glove will process the haptic
commands to match the resistance state of the robotic arm. Both the haptic glove and the robotic arm will be powered by Li-ion cells.
Overall, the user will place their right hand inside the haptic glove and control the robotic arm by changing the position of their right hand. Aside from visual sight, the robotic arm will make the user aware of resistance that it encounters through haptic feedback of the electromagnetic brakes.

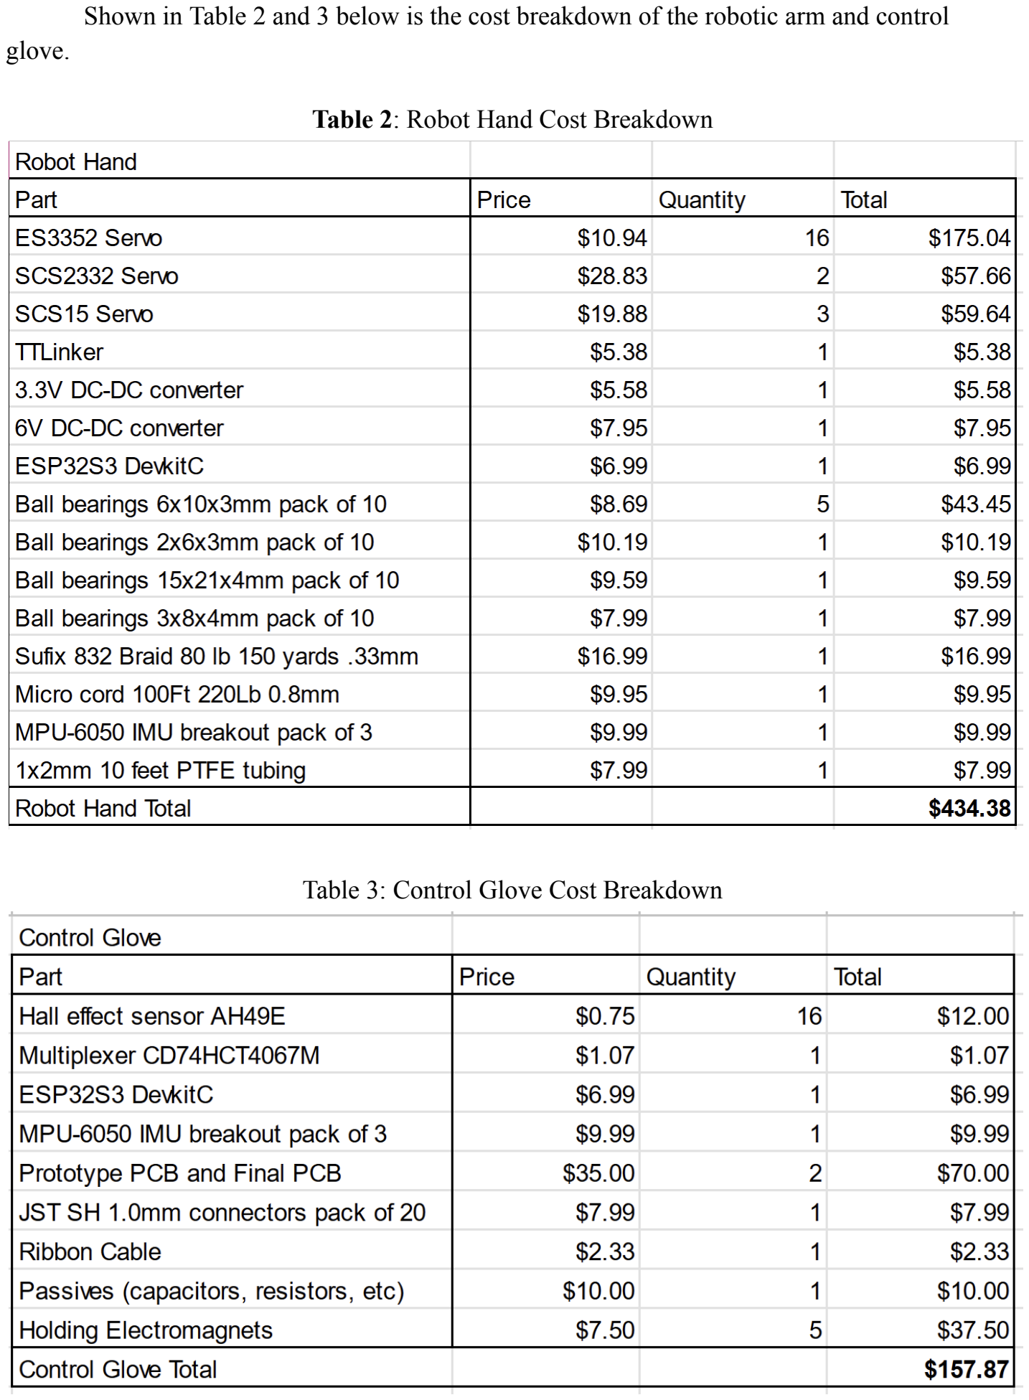
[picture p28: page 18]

Shown in Table 2 and 3 below is the cost breakdown of the robotic arm and control glove.

Table 2: Robot Hand Cost Breakdown

Table 3: Control Glove Cost Breakdown

Timeline

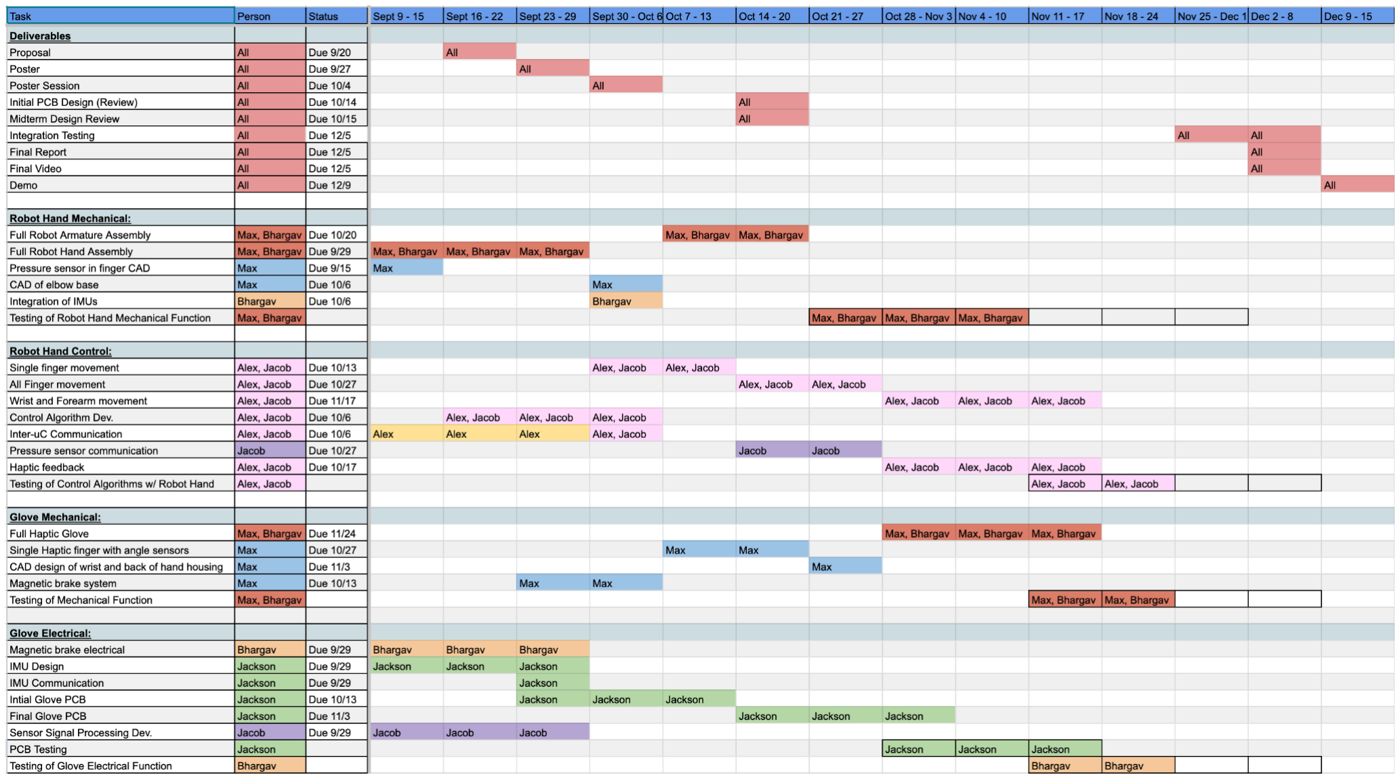
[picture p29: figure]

Figure 10: Gantt Chart

Figure 10 above showcases the Gantt Chart we will be following to keep us on track to meet our project goals. The main subtasks of our project are the development of the robot hand mechanical system, robot hand control algorithm, control glove mechanical system, and control glove electrical system.
We assigned responsibilities based on each of our strengths and knowledge bases, which led to the following. Since Max has extensive experience on the Solar Car team designing the suspension and thus sound knowledge in mechanical systems and CAD, his primary responsibility is the mechanical aspects of the control glove and robotic arm. Due to Bhargav’s background in electromagnetic fields through classes and projects, his responsibility is the haptic brake system using electromagnets; his secondary responsibility will be assisting Max with mechanical design due to expressed interest. Alex and Jacob are interested in control theory and signal processing and have extensive programming experience, which gives them the responsibility of developing the control algorithms and programming the microcontrollers. Since Jackson expressed interest in designing the PCBs and has additional experience through his internships, he will be overseeing the development of our circuit boards.
Each of the respective subsystems can be developed in parallel, but within each subsystem there are tasks that must be achieved periodically before moving on to the next. For example, the electrical aspect of the haptic brake system (electromagnetic brake) must be completed before it is mechanically implemented in the glove, since the electromagnet is the core function of the haptic brake. But overall, the majority of the tasks required for this project can be accomplished in parallel, with the limiting factor being time.

Expectations

Shown in Table 4 below is the rubric breakdown for this project. Table 5 is the grading scale associated with this rubric.

Table 4: Project Rubric Breakdown
Points | Robotic Arm | Glove Sensing | Glove Haptics | Control Alg.
3 | Complete movement of fingers, wrist, forearm, and elbow | Complete tracking of fingers, wrist, forearm, and elbow | The haptic glove provides real-time force feedback, replicating the resistance faced by the robotic arm. | Control algorithm allows for haptic glove mirroring and reasonably easy usage
2 | Complete movement of 2 or more of the fingers system, wrist, forearm, and elbow | Complete tracking of 2 or more of fingers, wrist, forearm, and elbow | The haptic glove provides real-time force feedback, replicating the resistance faced by the robotic arm, but there is a noticeable delay in the system | Control algorithm calibration provides some control over movements (robotic arm movement varies largely from glove movement)
1 | Partial movement of fingers, wrist, forearm, or elbow | Partial tracking of fingers, wrist, forearm, or elbow | The haptic response of the glove is inconsistent | Control algorithm is unstable or not robust
0 | There is no movement | There is no tracking | There is no haptic response | Control algorithm is not implemented

Table 5: Grading Scale
Points | Grade
11-12 | A+
8-10 | A
5-7 | B
3-4 | C
1-2 | D
0 | F

References

[1] “Gloves G1,” HaptX. Accessed: Sep. 20, 2024. [Online]. Available: https://haptx.com/gloves-g1/
[2] “SenseGlove for Virtual Reality prototyping,” SenseGlove. Accessed: Sep. 20, 2024. [Online]. Available:
https://www.senseglove.com/solutions/senseglove-for-virtual-prototyping/
[3] “WEART haptic solutions | WEART.” Accessed: Sep. 20, 2024. [Online]. Available:
https://weart.it/
[4] Lucas VRTech, How to build cheap VR Haptic Gloves to FEEL VR., (Jul. 10, 2022). Accessed: Sep. 20, 2024. [Online Video]. Available: https://www.youtube.com/watch?v=2yF-SJcg3zQ
[5] NepYope, I built VR Haptic Gloves to Control Robots, (Jul. 16, 2022). Accessed: Sep. 20, 2024. [Online Video]. Available: https://www.youtube.com/watch?v=iPtgvh6fNdQ
[6] “DexHand - An Open Source Dexterous Humanoid Robot Hand,” DexHand - An Open Source Dexterous Humanoid Robot Hand. Accessed: Sep. 20, 2024. [Online]. Available: https://www.dexhand.org/
[7] C. Knospe, “PID control.” IEEE, Feb. 2006. Accessed: Sep. 20, 2024. [Online]. Available: https://ieeexplore.ieee.org/document/1580151
[8] D. Eridani, A. F. Rochim, and F. N. Cesara, “Comparative Performance Study of ESP-NOW, Wi-Fi, Bluetooth Protocols based on Range, Transmission Speed, Latency, Energy Usage and Barrier Resistance.” IEEE, Sep. 2021. Accessed: Sep. 20, 2024. [Online]. Available: https://ieeexplore.ieee.org/document/9573246
[9] “Linear Hall-Effect IC Data Sheet.” BCD Semiconductor Manufacturing Limited, Aug. 2010. Accessed: Sep. 20, 2024. [Online]. Available: https://www.diodes.com/assets/Datasheets/AH49E.pdf
[10] F. Leens, “An introduction to I2C and SPI protocols,” IEEE Instrum. Meas. Mag., vol. 12, no. 1, pp. 8–13, Feb. 2009, doi: 10.1109/MIM.2009.4762946.
[11] “5V Electromagnet - 2.5 Kg Holding Force.” Adafruit. [Online]. Available: (https://www.zotero.org/google-docs/?RXBp5a)

https://mm.digikey.com/Volume0/opasdata/d220001/medias/docus/836/3872_Web.pdf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
[12] “3D printing and its environmental implications,” in The Next Production Revolution: Implications for Governments and Business, Paris: OECD, 2017, pp. 171–213. Accessed: Sep. 20, 2024. [Online]. Available: https://www.oecd-ilibrary.org/science-and-technology/the-next-production-revolution/3d-printing-and-its-environmental-implications_9789264271036-9-en
[13] “Electrical Enclosure Types - Non Hazardous Location Environmental Rating Standards Comparison.” NEMA Enclosures. Accessed: Sep. 20, 2024. [Online]. Available: https://www.nemaenclosures.com/media/pdf/NE-NEMA-vs-UL-012314.pdf
[14] “IEC 61000-6-8:2020.” IEC, Jul. 2020. Accessed: Sep. 20, 2024. [Online]. Available: https://webstore.iec.ch/en/publication/62839
[15] “ISO 9241-940:2017.” ISO, Nov. 2017. Accessed: Sep. 20, 2024. [Online]. Available: https://www.iso.org/standard/61362.html
[16] “ISO 10218-1:2011.” ISO, Jul. 2011. Accessed: Sep. 20, 2024. [Online]. Available: https://www.iso.org/standard/51330.html (https://www.zotero.org/google-docs/?RXBp5a)

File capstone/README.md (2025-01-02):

## ECE 4440 Capstone Design Fall 2024

This directory contains Team Dexterity's deliverables for ECE 4440 Design, Fall 2024. This course serves as the capstone engineering design experience for UVA's Electrical and Computer Engineering Department. The course focuses on teamwork, project management, and technical problem-solving to design and build a functional prototype for a defined end-user. Teams work within a $500 budget using microcontrollers, PCBs, or FPGAs while addressing global, cultural, and societal factors. Deliverables include a project proposal, a poster presentation, a midterm design review,a final report, a video demo, and a live demo day presentation. 

### Requirements 
  - `ProjectProposal_24F.pdf` - the project proposal requirements
  - `CapstoneFinalProjectReport_24F.pdf` - the final report requirements
  - `CapstoneFinalProjectVideo_24F.pdf` - the video demo requirements

### Reports
  - `ProjectProposal_Dexterity.pdf` - our proposal for the project
  - `Poster_Dexterity.pdf` - our poster presentation for the project
  - `MidtermDesignReview_Dexterity.pdf` - our midterm design review for the project
  - `CapstoneFinalReport_Dexterity.pdf` - our final report for the project
  
The final video is available in this [Google Drive Link](https://drive.google.com/file/d/1M35dVxJw4dA2zivvejlQ71bkoA-sMLWy/view?usp=drive_link)

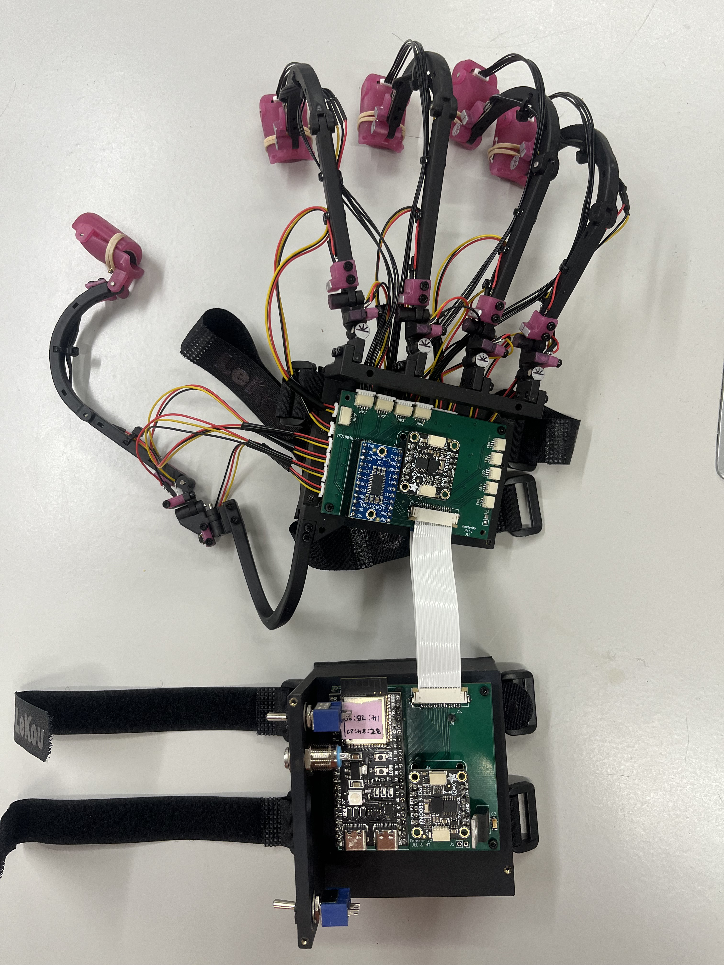
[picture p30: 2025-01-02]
media/images/glove_v2_top_down.jpeg

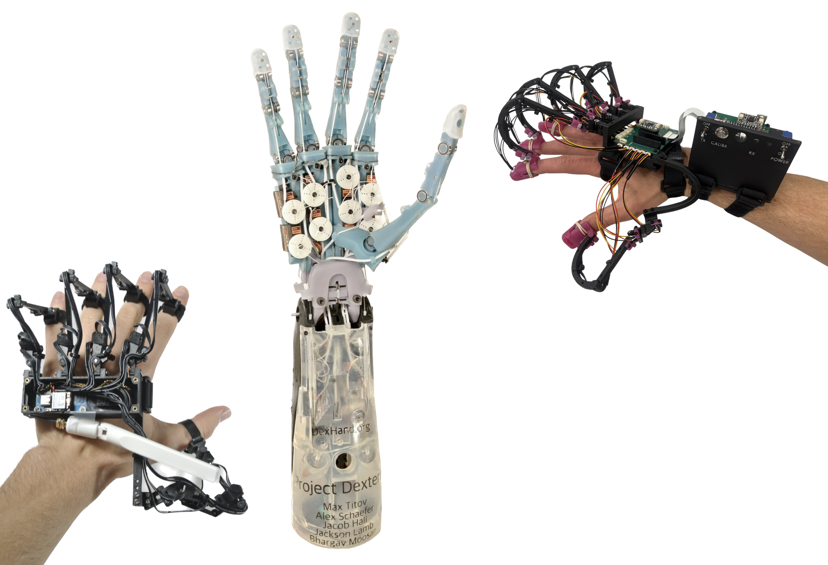
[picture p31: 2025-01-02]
media/images/main_github_pic.png

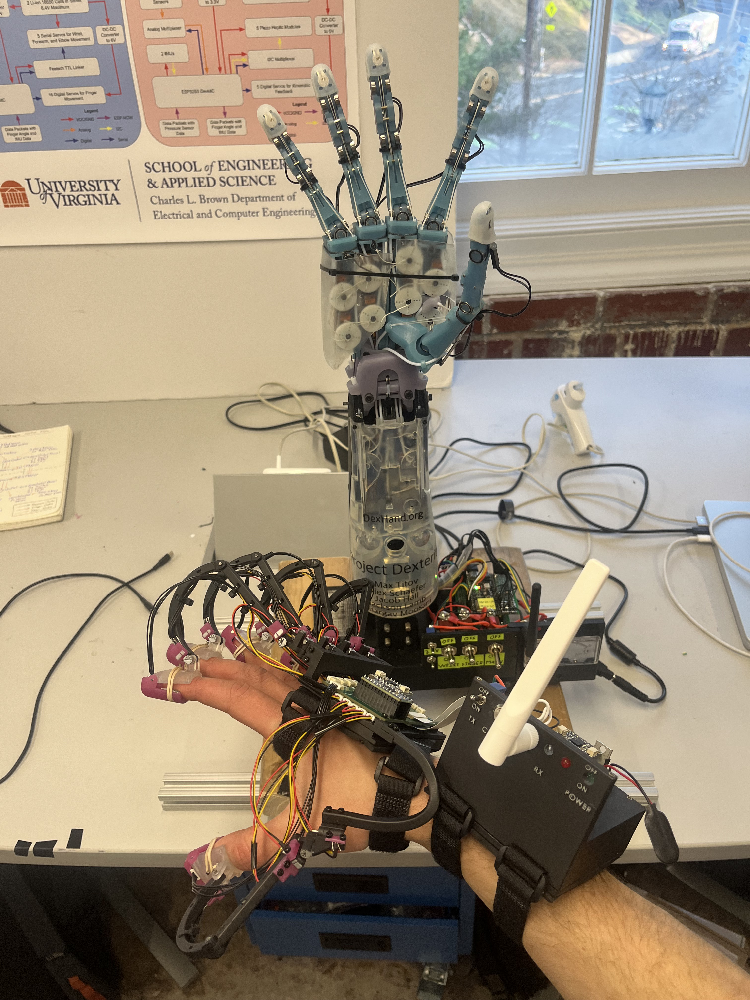
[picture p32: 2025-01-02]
media/images/V2_glove_and_hand.jpeg

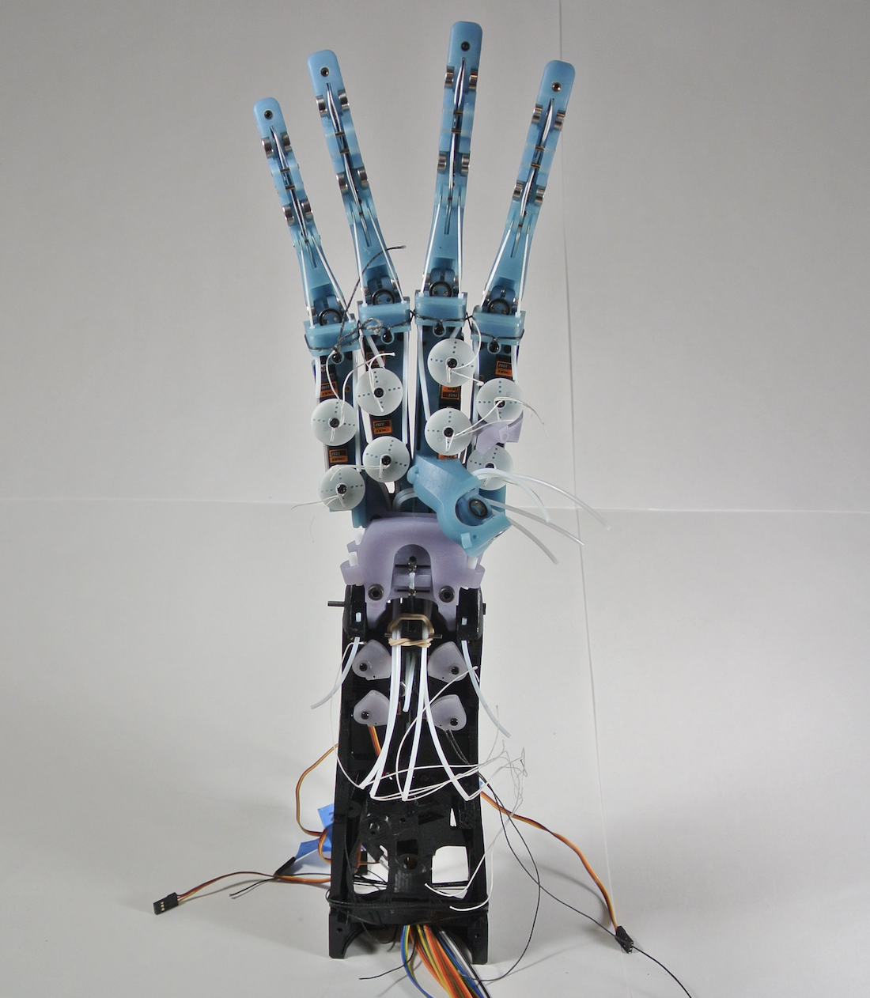
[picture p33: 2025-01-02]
media/images/hand_progress.png

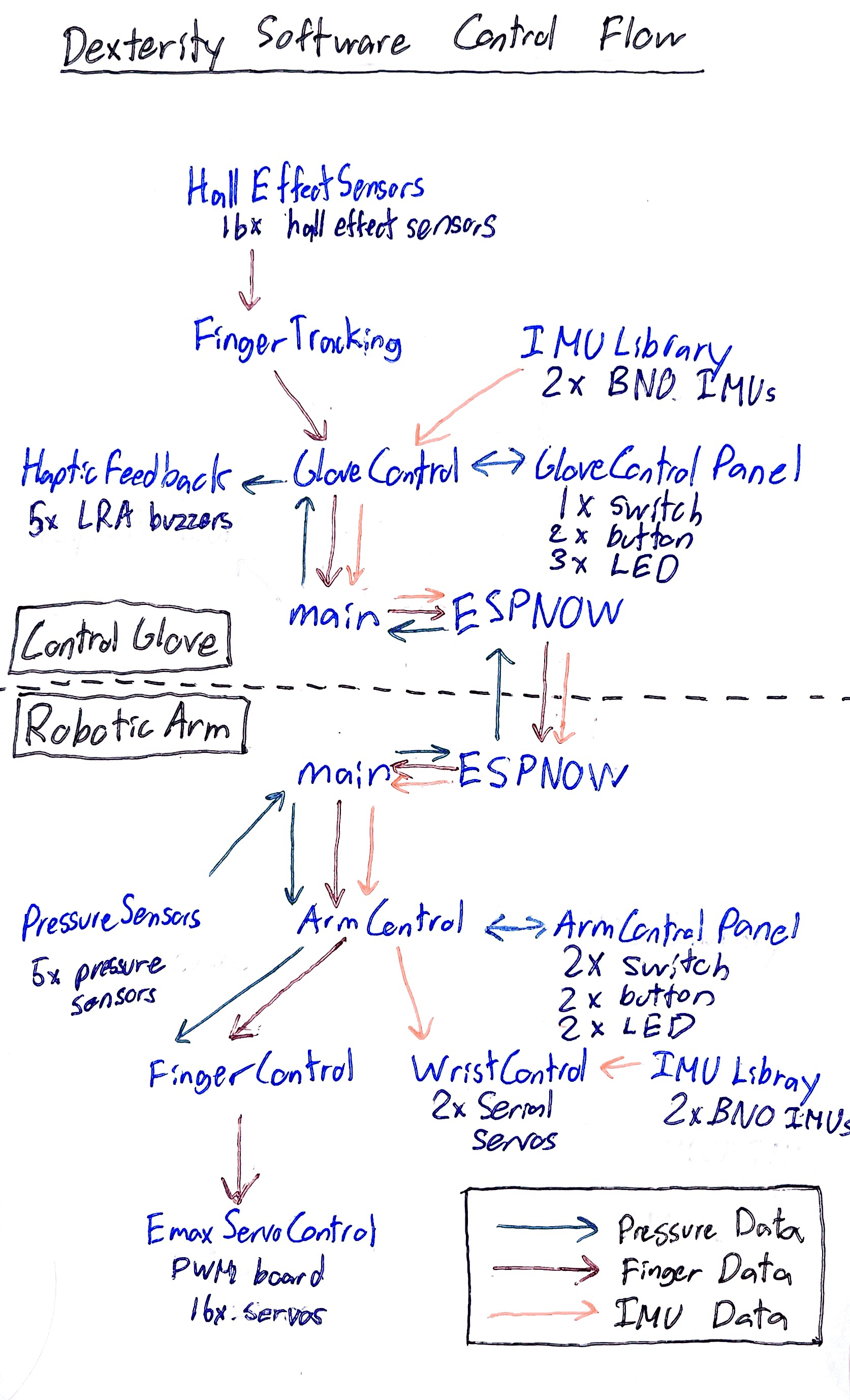
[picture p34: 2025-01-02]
media/diagrams/software_data_flow.png

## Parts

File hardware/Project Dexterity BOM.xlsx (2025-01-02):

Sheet: Robotic Arm BOM
 | Robotic Arm BOM
 | Part | Price | Quantity | Total | Link | Notes | Required/Nice to have
mechanical | various M2 and M3 screws |  |  | 0 |  | see General BOM sheet | Required
 | various M2 and M3 threaded inserts |  |  | 0 |  | see General BOM sheet | Required
 | 2mm stainless steel rods |  |  | 0 |  | see General BOM sheet | Required
 | Ball bearings 6x10x3mm pack of 10 | 8.69 | 5 | 43.45 | https://www.amazon.com/uxcell-MR106-2RS-Groove-Bearings-Double/dp/B082PSCNKB | bearings for fingers. exactly 50 are needed so I recommend ordering an extra set | Required
 | Ball bearings 2x6x3mm pack of 10 | 10.19 | 1 | 10.19 | https://amzn.to/3yYlTHg | bearings for wrist | Required
 | Ball bearings 15x21x4mm pack of 10 | 9.59 | 1 | 9.59 | https://amzn.to/3TsMSTO | bearings for wrist | Required
 | Ball bearings 3x8x4mm pack of 10 | 7.99 | 1 | 7.99 | https://amzn.to/3VyE28O | bearings for wrist | Required
 | Sufix 832 Braid 80 lb 150 yards .33mm | 16.99 | 1 | 16.99 | https://amzn.to/3DgjNoF | fishing line for finger tendons | Required
 | Micro cord 100Ft 220Lb 0.8mm | 9.95 | 1 | 9.95 | https://amzn.to/3GMKQJL (https://www.amazon.com/emma-kites-220lbs-Braided-Polyethylene/dp/B0829KT3FV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) | Slightly thicker 0.8mm kiteline for the finger ligaments and wrist tendons | Required
 | 1x2mm 10 feet PTFE tubing | 7.99 | 1 | 7.99 | https://www.amazon.com/Quickun-Teflon-Tubing-Printer-Length/dp/B08Q83XNTT | tubing for tendons | Required
 | 2x4mm 5 feet PTFE tubing | 7.99 | 1 | 7.99 | https://www.amazon.com/Teflon-tubing-Filament-Printer-Tech/dp/B073RDFTDV?s=industrial | tubing for wrist. standard size for 3d printer filament tubing (I just took some from a broken 3d printer) | Required
 | Stainless Steel Tension Spring Extension Spring Out Dia 2mm 5 Pieces 3.28Ft | 13 | 1 | 13 | https://www.amazon.com/dp/B0C85SCR7T?ref=ppx_yo2ov_dt_b_fed_asin_title&th=1 | for tensioning fingers | Required
 | M3 x 0.5 mm Thread, 70 mm Long bolt | 4.26 | 2 | 8.52 | https://www.mcmaster.com/91290A297/ | connects wrist assembly to hand and to forearm | Required
 | M4 x 0.7 mm Thread, 40 mm Long, Fully Threaded (pack of 5) | 3 | 1 | 3 | https://www.mcmaster.com/91290A174/ | holds wrist assembly together | Required
 | Knurled Insert Nuts, M2 x 4mm(L) x 3.5mm(OD) | 6.69 | 1 | 6.69 | https://www.amazon.com/dp/B07R6M8DC9?ref=ppx_yo2ov_dt_b_fed_asin_title&th=1 | threaded inserts to wrap fingertip tendons around | Required
 | M4× Stainless Steel Socket Cap Nut | 9.99 | 1 | 9.99 | https://www.amazon.com/dp/B0CKSDJ68N?ref=ppx_yo2ov_dt_b_fed_asin_title&th=1 | not necessary but makes the wrist assembly lower profile | Nice to have
 | Guitair fingertip protectors | 7.99 | 1 | 7.99 | https://www.amazon.com/dp/B08113SYL9?ref=ppx_yo2ov_dt_b_fed_asin_title&th=1 | adds a lot of grip to the fingertips (smallest size worked well for all fingers except it slightly slipped off of pinkie) | Nice to have
electrical | EMAX ES3352 Servo | 8.84 | 16 | 141.44 | https://www.aliexpress.us/item/3256804528206794.html?gatewayAdapt=glo2usa | servos for finger movement, prone to burnout | Required
 | 16 Channel 12-Bit PWM Servo Motor Driver | 8.99 | 1 | 8.99 | https://www.amazon.com/dp/B01D1D0CX2?ref=ppx_yo2ov_dt_b_fed_asin_title | pwm board for EMAX servos | Required
 | Feetech SCS2332 Servo | 28.83 | 2 | 57.66 | https://www.aliexpress.us/item/3256801551680860.html?gatewayAdapt=glo2usa | serial servos for wrist movement | Required
 | Feetech SCS15 Servo | 19.88 | 1 | 19.88 | https://www.aliexpress.us/item/3256801550976120.html?gatewayAdapt=glo2usa | serial servo for forearm rotation | Nice to have
 | TTLinker | 7.05 | 1 | 7.05 | https://www.aliexpress.us/item/3256803821610559.html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: | serial conversion board for feetech serial servos | Required
 | ESP32S3 DevkitC | 4.04 | 1 | 4.04 | https://www.aliexpress.us/item/3256804859409648.html?gatewayAdapt=glo2usa | microcontroller to control system | Required
 | 6V 10A wall power supply | 16.99 | 1 | 16.99 | https://www.amazon.com/inShareplus-Voltage-Transformer-100-240V-Connector/dp/B01GHN2S7Q | most the system drew is around 5 amps so this has good overhead | Required
 | 3.3V DC-DC converter | 1.59 | 1 | 1.59 | https://www.digikey.com/en/products/detail/texas-instruments/LM1117T-3-3-NOPB/363593 | needed if you want to power micro from wall supply | Nice to have
 | 12 Volt DC 30A Heavy Duty 3 Way Toggle Switch | 9.99 | 1 | 9.99 | https://www.amazon.com/dp/B0BHY1CY72?ref=ppx_yo2ov_dt_b_fed_asin_title&th=1 | way overkill for the amperage needed | Nice to have
 | pressure sensors (FSR05BE) | 6.59 | 5 | 32.95 | https://www.digikey.com/en/products/detail/ohmite/FSR05BE/10127621 | FSRs that go on fingertips of robotic hand to drive haptic feedback | Nice to have
 | 2 pos 28 guage wire 25ft | 10.48 | 1 | 10.48 | https://www.amazon.com/BNTECHGO-Silicone-Ribbon-Flexible-Strand/dp/B09X483BL1 | wires for FSRs | Nice to have
 | DC 0-10A Rectangular Analog Ampere | 8.99 | 1 | 8.99 | https://www.amazon.com/dp/B077CM86VF?ref=ppx_yo2ov_dt_b_fed_asin_title | to show amperage draw of entire system | Nice to have
 | various switches and leds |  |  |  |  | for the control panel | Nice to have
 | Robotic Arm Total |  |  | 483.38

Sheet: Control Glove BOM
 | Control Glove BOM
 | Part | Price | Quantity | Total | Link | Notes | Required/Nice to have
mechanical | various M2 screws |  |  |  |  | see General BOM sheet | Required
 | M2 threaded inserts |  |  |  |  | see General BOM sheet | Required
 | 2mm stainless steel rods |  |  |  |  | see General BOM sheet | Required
 | rubber bands |  |  |  |  | to hold finger buckets to fingers | Required
 | 4mm thick foam | 9.99 | 1 | 9.99 | https://www.amazon.com/dp/B0B53D7X5R?ref=ppx_yo2ov_dt_b_fed_asin_title&th=1 | to go between 3d printed part and skin for comfort | Nice to have
electrical | Hall effect sensor AH49E | 12.95 | 1 | 12.95 | https://www.amazon.com/dp/B0BXDMRHF8?th=1 | 16 needed but extras are always nice | Required
 | ESP32S3 DevkitC | 6.99 | 1 | 6.99 | https://www.aliexpress.us/item/3256804859409648.html?gatewayAdapt=glo2usa | microcontroller to control system | Required
 | LRA Driver Wireling (haptic module) | 14.95 | 5 | 74.75 | https://tinycircuits.com/products/lra-wireling-drv2605 | Buzzers for fingertips (these are kinda expensive, but are small and have a nice arduinio library for effects) | Required
 | 5x 200mm 5 pin JST SH | 3.99 | 1 | 3.99 | https://tinycircuits.com/products/5-pin-extension-cable?variant=30950352617556 | JST wires to connect buzzers to buzzers | Required
 | 20 Sets Mini Micro Sh 1.0mm Jst 3-Pin Connector Male | 7.99 | 1 | 7.99 | https://www.amazon.com/Micro-1-0mm-3-Pin-Connector-Female/dp/B09GP9S1W7 | 20x 3-pin JST cables (these are bad, too thin and prone to breaking. I also think they picked up EMF noise) | Required
 | Adafruit 9-DOF Orientation IMU Fusion Breakout - BNO085 | 24.95 | 2 | 49.9 | https://www.adafruit.com/product/4754 | 9 DOF IMU with onboard sensor fusion | Required
(the digikey parts show the exact amount needed. I recommend ordering extras) | 399-3676-1-ND | 0.5 | 1 | 0.5 | https://www.digikey.com/en/products/detail/kemet/T491A104K035AT/818537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 | bypass cap for Hall effect max | Required
 | 399-5179-1-ND | 0.49 | 2 | 0.98 | https://www.digikey.com/en/products/detail/kemet/T495A106K010ATE1K8/1829902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 | Input/output caps for voltage regulator | Required
 | 13-RC0402JR-1310KLCT-ND | 0.011 | 6 | 0.066 | https://www.digikey.com/en/products/detail/yageo/RC0402JR-1310KL/13694115 | Resistors | Required
 | 296-29408-1-ND | 0.58 | 1 | 0.58 | https://www.digikey.com/en/products/detail/texas-instruments/CD74HC4067M96/1507236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 | Hall effect mux | Required
 | LM1117T-3.3/NOPB-ND | 1.59 | 1 | 1.59 | https://www.digikey.com/en/products/detail/texas-instruments/LM1117T-3-3-NOPB/363593 | 3.3V voltage regulator | Required
 | 900-0152670315-ND | 2.58 | 2 | 5.16 | https://www.digikey.com/en/products/detail/molex/0152670315/4143361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 | ribbon cables | Required
 | WM10951CT-ND | 2 | 4 | 8 | https://www.digikey.com/en/products/detail/molex/0522071633/4444513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 | Ribbon cable connectors | Required
 | 455-SM03B-SRSS-TBCT-ND | 0.475 | 26 | 12.35 | https://www.digikey.com/en/products/detail/jst-sales-america-inc/SM03B-SRSS-TB/926709 | 3-pin JST connectors (10 of these are for resitive force feedback using servos and potentiometers which I never got around to implementing) | Required
 | 455-SM05B-SRSS-TBCT-ND | 0.86 | 5 | 4.3 | https://www.digikey.com/en/products/detail/jst-sales-america-inc/SM05B-SRSS-TB/926711 | 5-pin JST connectors | Required
 | various buttons, switches, and leds |  |  |  |  | for the control panel | Nice to have
 | Control Glove Total |  |  | 200.086

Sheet: General BOM
General BOM
Part | Price | Quantity | Total | Link | Notes
20 Pieces 2.0mm x 100mm 304 Stainless Steel Rods | 8.99 | 1 | 8.99 | https://www.amazon.com/dp/B09W5PT49F?ref=ppx_yo2ov_dt_b_fed_asin_title&th=1 | I used a dremel to cut these to length. you can also buy a kit with various lengths
Metric Threaded Inserts M2 M2.5 M3 M4 M5 M6 | 19.99 | 1 | 19.99 | https://www.amazon.com/dp/B0CN23ZKYN?ref=ppx_yo2ov_dt_b_fed_asin_title | I only used the M2 and M3 inserts from this kit. you can probably find a better kit
660 Pcs M2 Screws, M2*4mm/6mm/8mm/10mm/12mm/16mm | 8.99 | 1 | 8.99 | https://www.amazon.com/dp/B0B93G1H9L?ref=ppx_yo2ov_dt_b_fed_asin_title&th=1 | These are prone to stripping. I'm considering using torx M2s in future designs
340 Pcs M3 Screw Kit | 9.59 | 1 | 9.59 | https://www.amazon.com/dp/B0B5153SLD?ref=ppx_yo2ov_dt_b_fed_asin_title&th=1 | Also might transition to torx in the future
dupont wire variety pack | 6.98 | 1 | 6.98 | https://www.amazon.com/dp/B01EV70C78?ref=ppx_yo2ov_dt_b_fed_asin_title | Used in the robotic arm wiring
Proto pcb board kit | 13.99 | 1 | 13.99 | https://www.amazon.com/dp/B07NM68FXK?ref=ppx_yo2ov_dt_b_fed_asin_title | used one protopcb for the robotic arm electrical
General BOM Total |  |  | 68.53

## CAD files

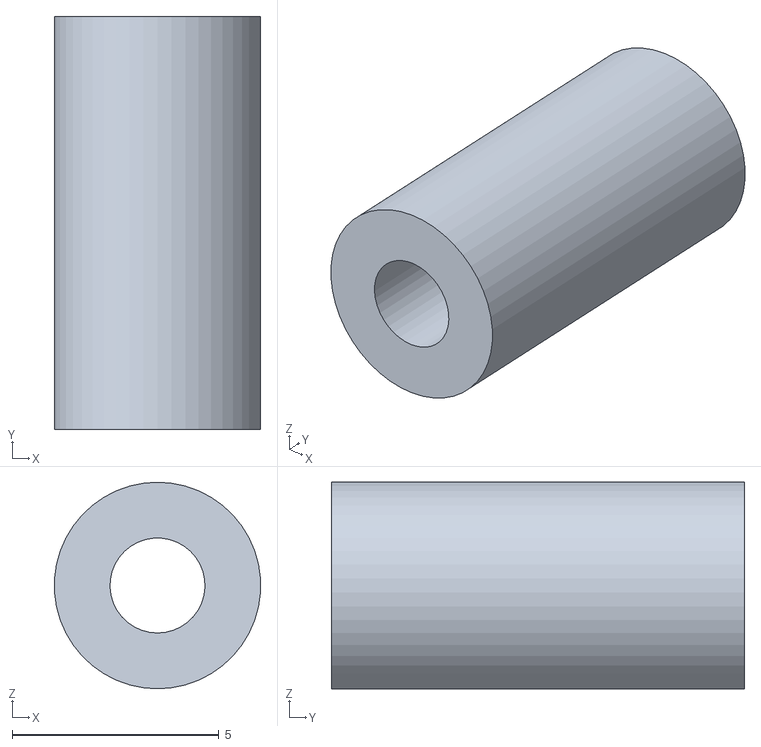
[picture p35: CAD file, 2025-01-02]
hardware/cad/arm base/arm base stl/standoff.STL
4.99 x 10.0 x 5.00

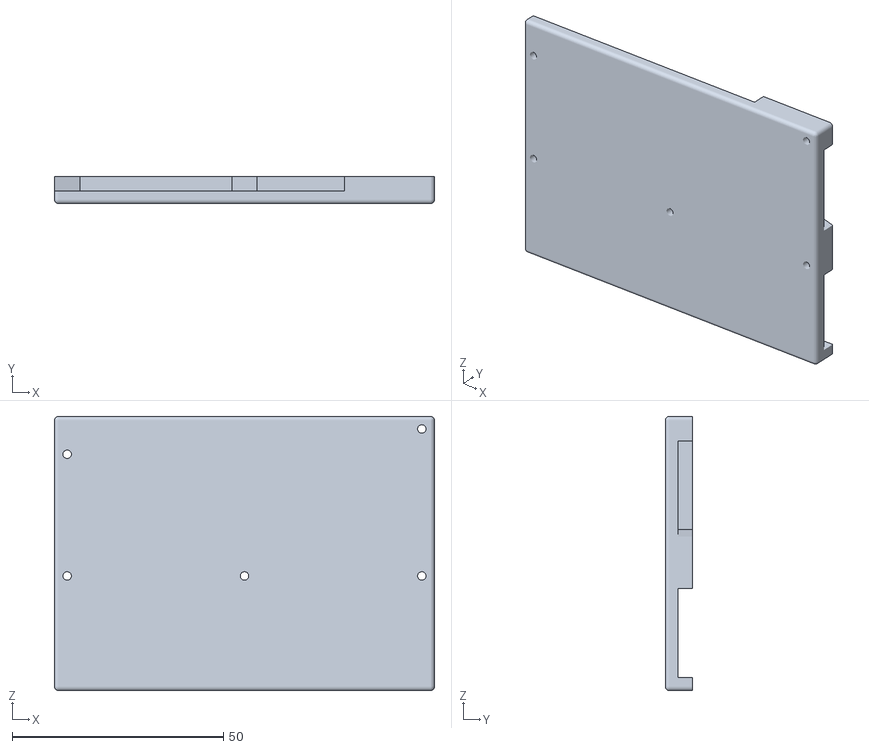
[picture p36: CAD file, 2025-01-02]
hardware/cad/glove v2.4/v2.4 enclosures stl/hand enclosure bottom v4.STL
90.0 x 6.50 x 65.0

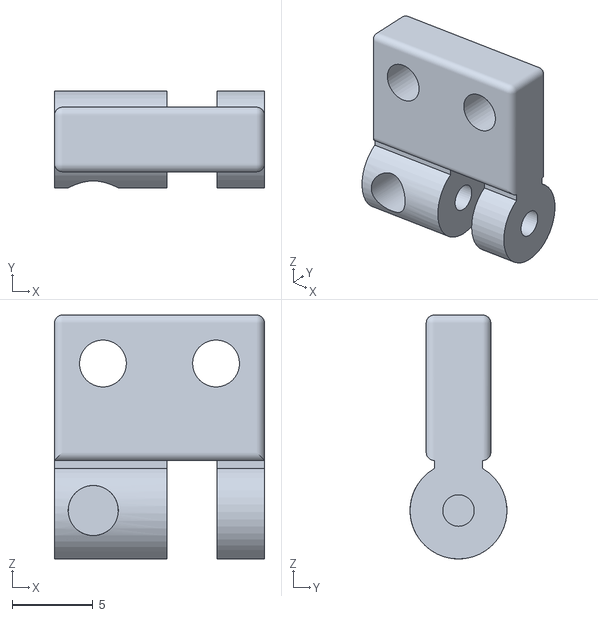
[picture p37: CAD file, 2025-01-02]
hardware/cad/glove v2.4/v2.4 fingers and thumb stl/mcp abduction joint v4.STL
13.0 x 6.00 x 15.1

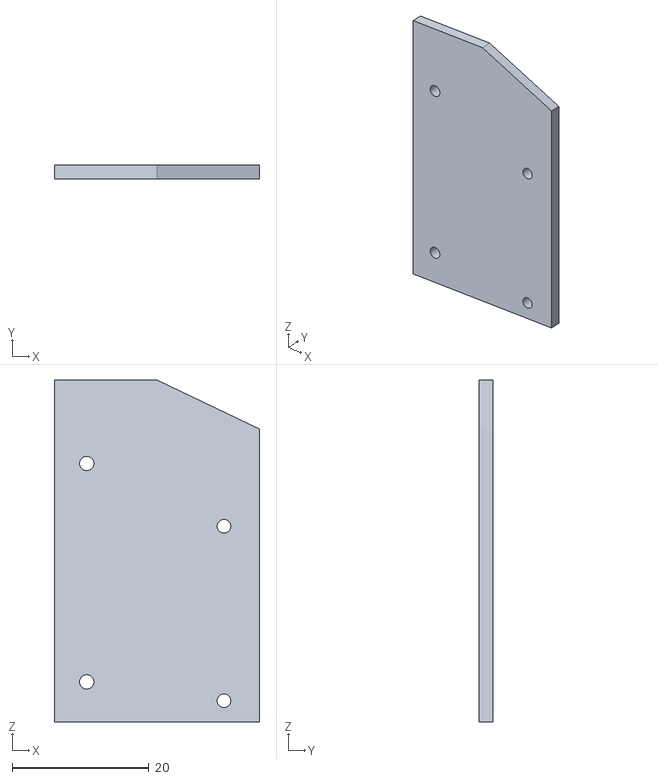
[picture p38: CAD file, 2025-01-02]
hardware/cad/arm base/arm base stl/dexhand shell zipper.STL
30.0 x 2.00 x 50.0

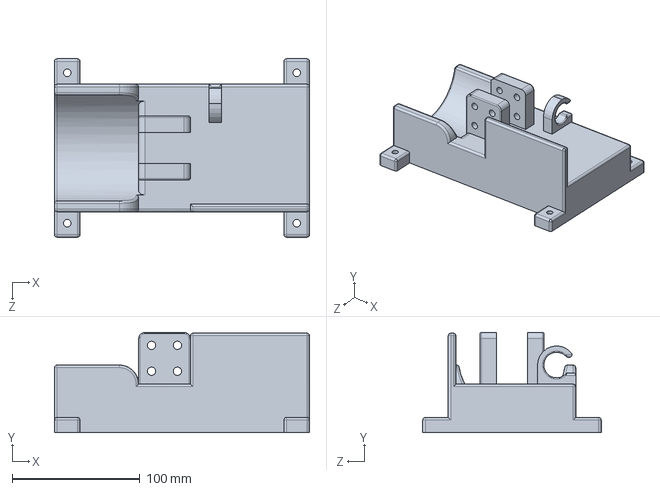
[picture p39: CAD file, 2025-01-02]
hardware/cad/arm base/arm base.SLDPRT
200.0 x 78.6 x 140.0 mm

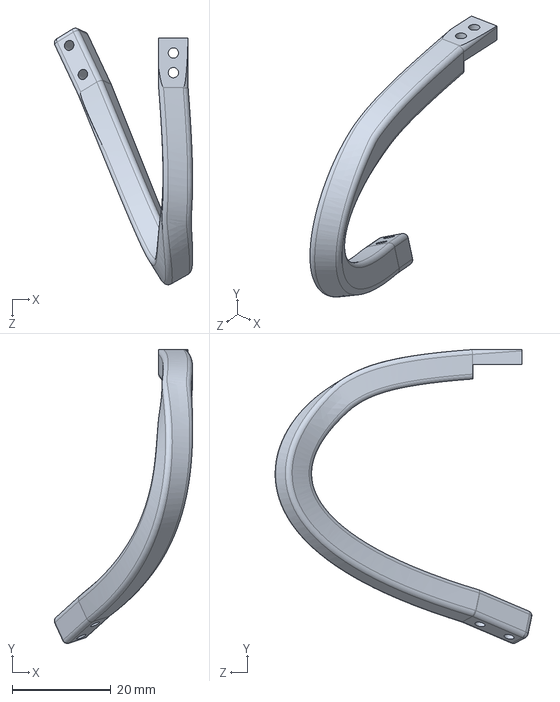
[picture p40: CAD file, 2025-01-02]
hardware/cad/glove v2.4/thumb attachment v4.SLDPRT
28.1 x 59.7 x 52.1 mm

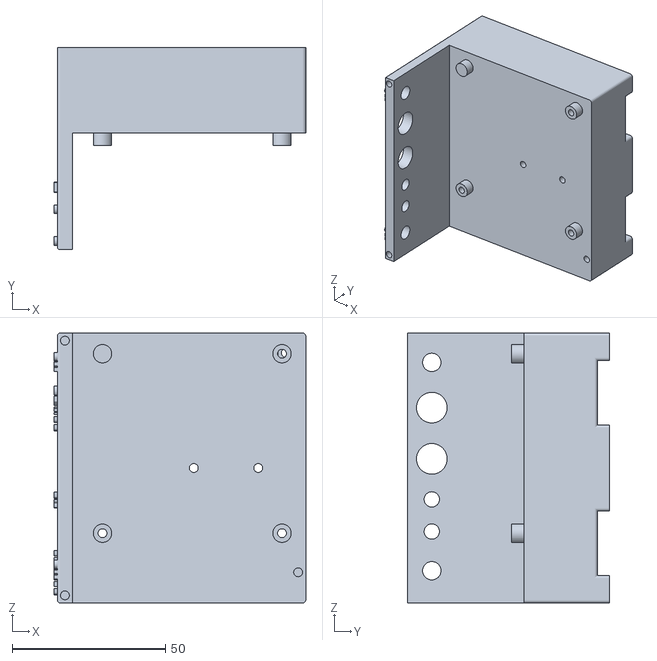
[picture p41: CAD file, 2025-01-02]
hardware/cad/glove v2.4/v2.4 enclosures stl/forearm enclosure middle v4.STL
82.0 x 66.0 x 88.0

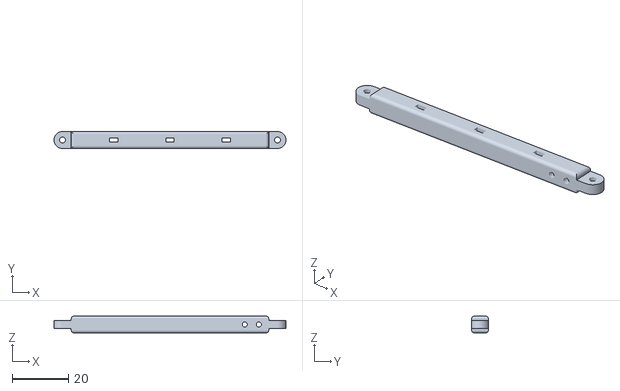
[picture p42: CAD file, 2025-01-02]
hardware/cad/glove v2.4/v2.4 fingers and thumb stl/straight arm v3 70mm.STL
82.2 x 6.00 x 6.00

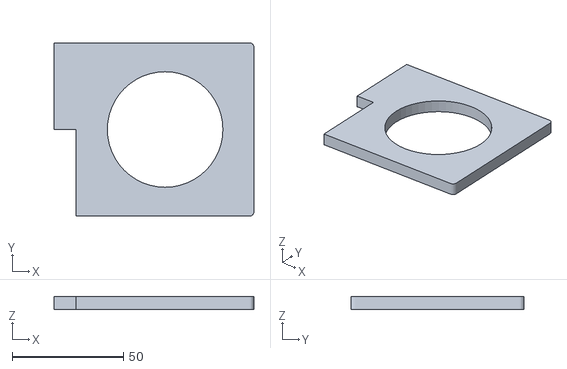
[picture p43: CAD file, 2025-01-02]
hardware/cad/arm base/arm base stl/amp meter holder.STL
90.0 x 78.0 x 6.00

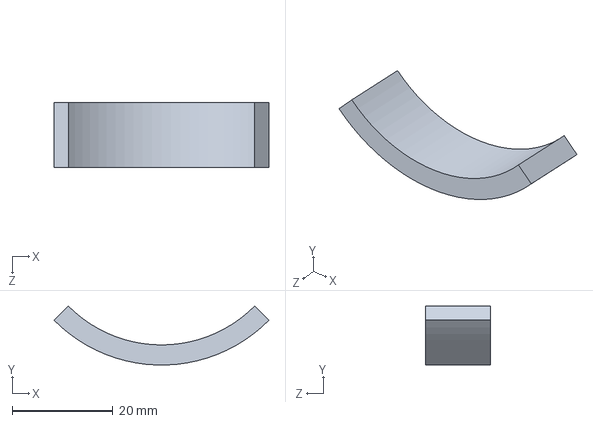
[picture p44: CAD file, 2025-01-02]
hardware/cad/arm base/wire holder.SLDPRT
42.7 x 11.7 x 13.0 mm

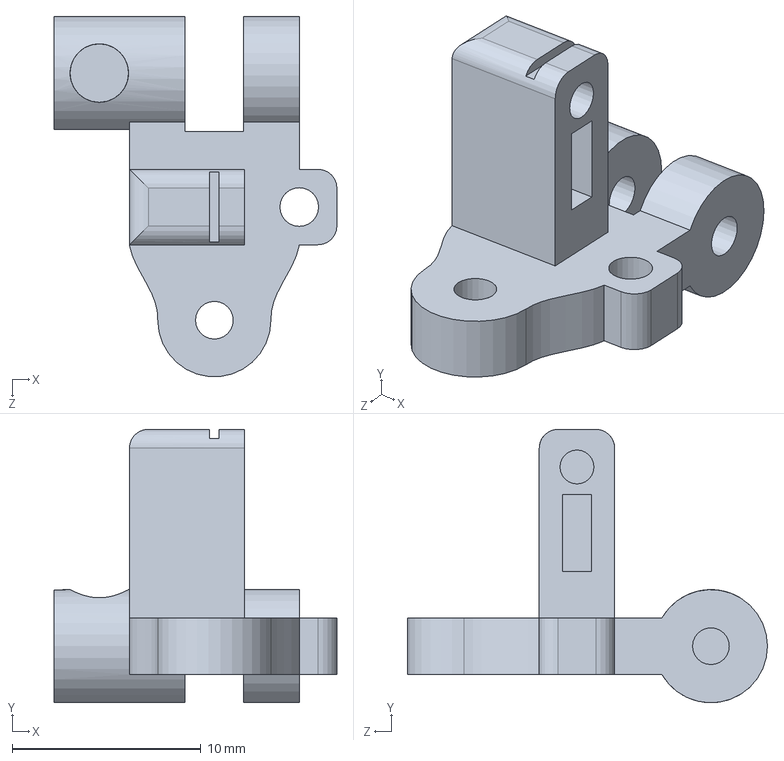
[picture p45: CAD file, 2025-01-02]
hardware/cad/glove v2.4/thumb mcp flex joint v4.SLDPRT
15.0 x 14.5 x 19.1 mm

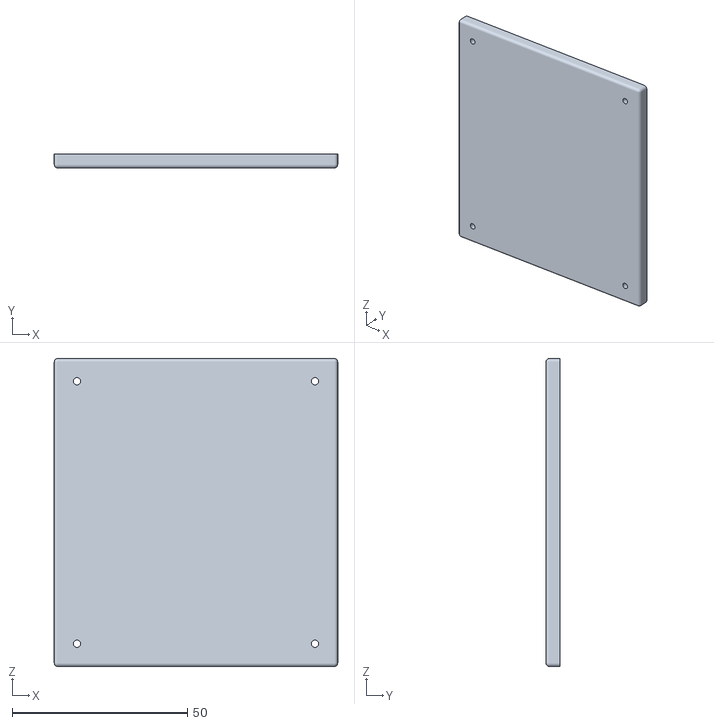
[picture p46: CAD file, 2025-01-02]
hardware/cad/glove v2.4/v2.4 enclosures stl/forearm enclosure bottom v4.STL
81.0 x 4.00 x 88.0

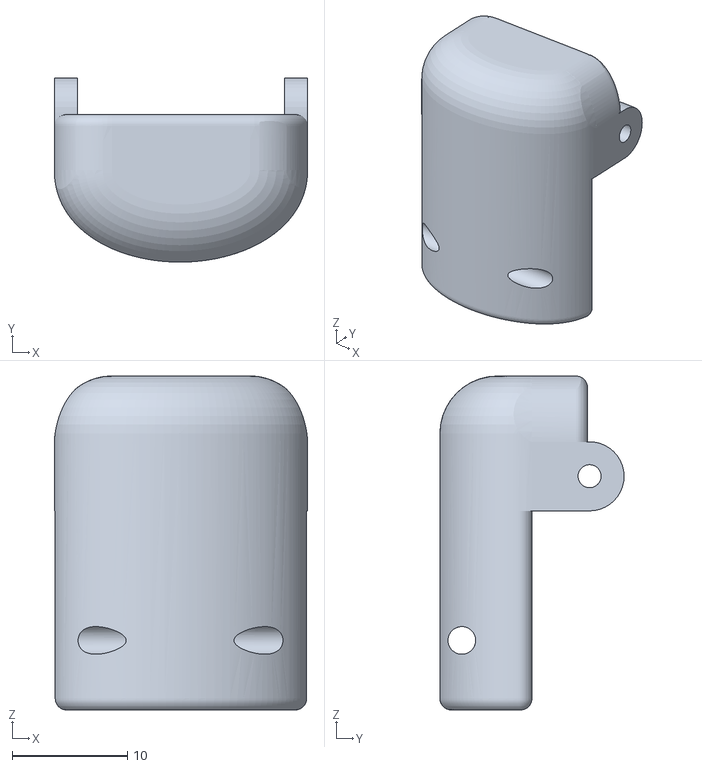
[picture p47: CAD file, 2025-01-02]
hardware/cad/glove v2.4/v2.4 fingers and thumb stl/finger lower v4.STL
22.0 x 16.0 x 29.0

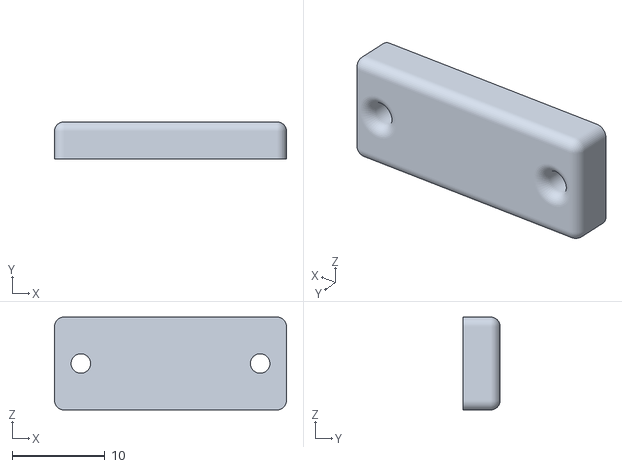
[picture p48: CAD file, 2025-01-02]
hardware/cad/arm base/arm base stl/wire holder flat.STL
25.0 x 4.00 x 10.0

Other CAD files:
hardware/cad/glove v2.4/Thumb joint.SLDASM
hardware/cad/arm base/standoff.SLDPRT
hardware/cad/arm base/wire holder flat.SLDPRT
hardware/cad/glove v2.4/thumb attachment rod.SLDPRT
hardware/cad/arm base/amp meter holder.SLDPRT
hardware/cad/arm base/arm base stl/arm base v2.STL
hardware/cad/arm base/arm base stl/wire holder.STL
hardware/cad/arm base/dexhand shell zipper.SLDPRT
hardware/cad/glove v2.4/finger upper v4.SLDPRT
hardware/cad/glove v2.4/forearm enclosure bottom v4.SLDPRT
hardware/cad/glove v2.4/forearm enclosure middle v4.SLDPRT
hardware/cad/glove v2.4/forearm enclosure top v4.SLDPRT
hardware/cad/glove v2.4/hand enclosure bottom v4.SLDPRT
hardware/cad/glove v2.4/hand enclosure middle v4.1.SLDPRT
hardware/cad/glove v2.4/hand enclosure middle v4.SLDPRT
hardware/cad/glove v2.4/hand enclosure top.SLDPRT
hardware/cad/glove v2.4/mcp flex joint sensor holder v4.SLDPRT
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

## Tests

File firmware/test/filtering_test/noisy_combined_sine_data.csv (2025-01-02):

Time | Data
0.000000000000000000e+00 | 1.200000000000000000e+02
2.000000000000000042e-02 | 1.158616048324729491e+02
4.000000000000000083e-02 | 1.217079019392407702e+02
5.999999999999999778e-02 | 1.285236688055636023e+02
8.000000000000000167e-02 | 1.312938528549188959e+02
1.000000000000000056e-01 | 1.270036552115755342e+02
1.199999999999999956e-01 | 1.406386130230065135e+02
1.400000000000000133e-01 | 1.431846798748394463e+02
1.600000000000000033e-01 | 1.496283038418825697e+02
1.799999999999999933e-01 | 1.449565027321951334e+02
2.000000000000000111e-01 | 1.461569360971203650e+02
2.200000000000000011e-01 | 1.582179735985748152e+02
2.399999999999999911e-01 | 1.581287593455848253e+02
2.600000000000000089e-01 | 1.478792718349648112e+02
2.800000000000000266e-01 | 1.634603791560075194e+02
2.999999999999999889e-01 | 1.588638891459662545e+02
3.200000000000000067e-01 | 1.530825942117990053e+02
3.400000000000000244e-01 | 1.551103105639489570e+02
3.599999999999999867e-01 | 1.599419116396863387e+02
3.800000000000000044e-01 | 1.605733555265517509e+02
4.000000000000000222e-01 | 1.660017062305302318e+02
4.199999999999999845e-01 | 1.732251486685596547e+02
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

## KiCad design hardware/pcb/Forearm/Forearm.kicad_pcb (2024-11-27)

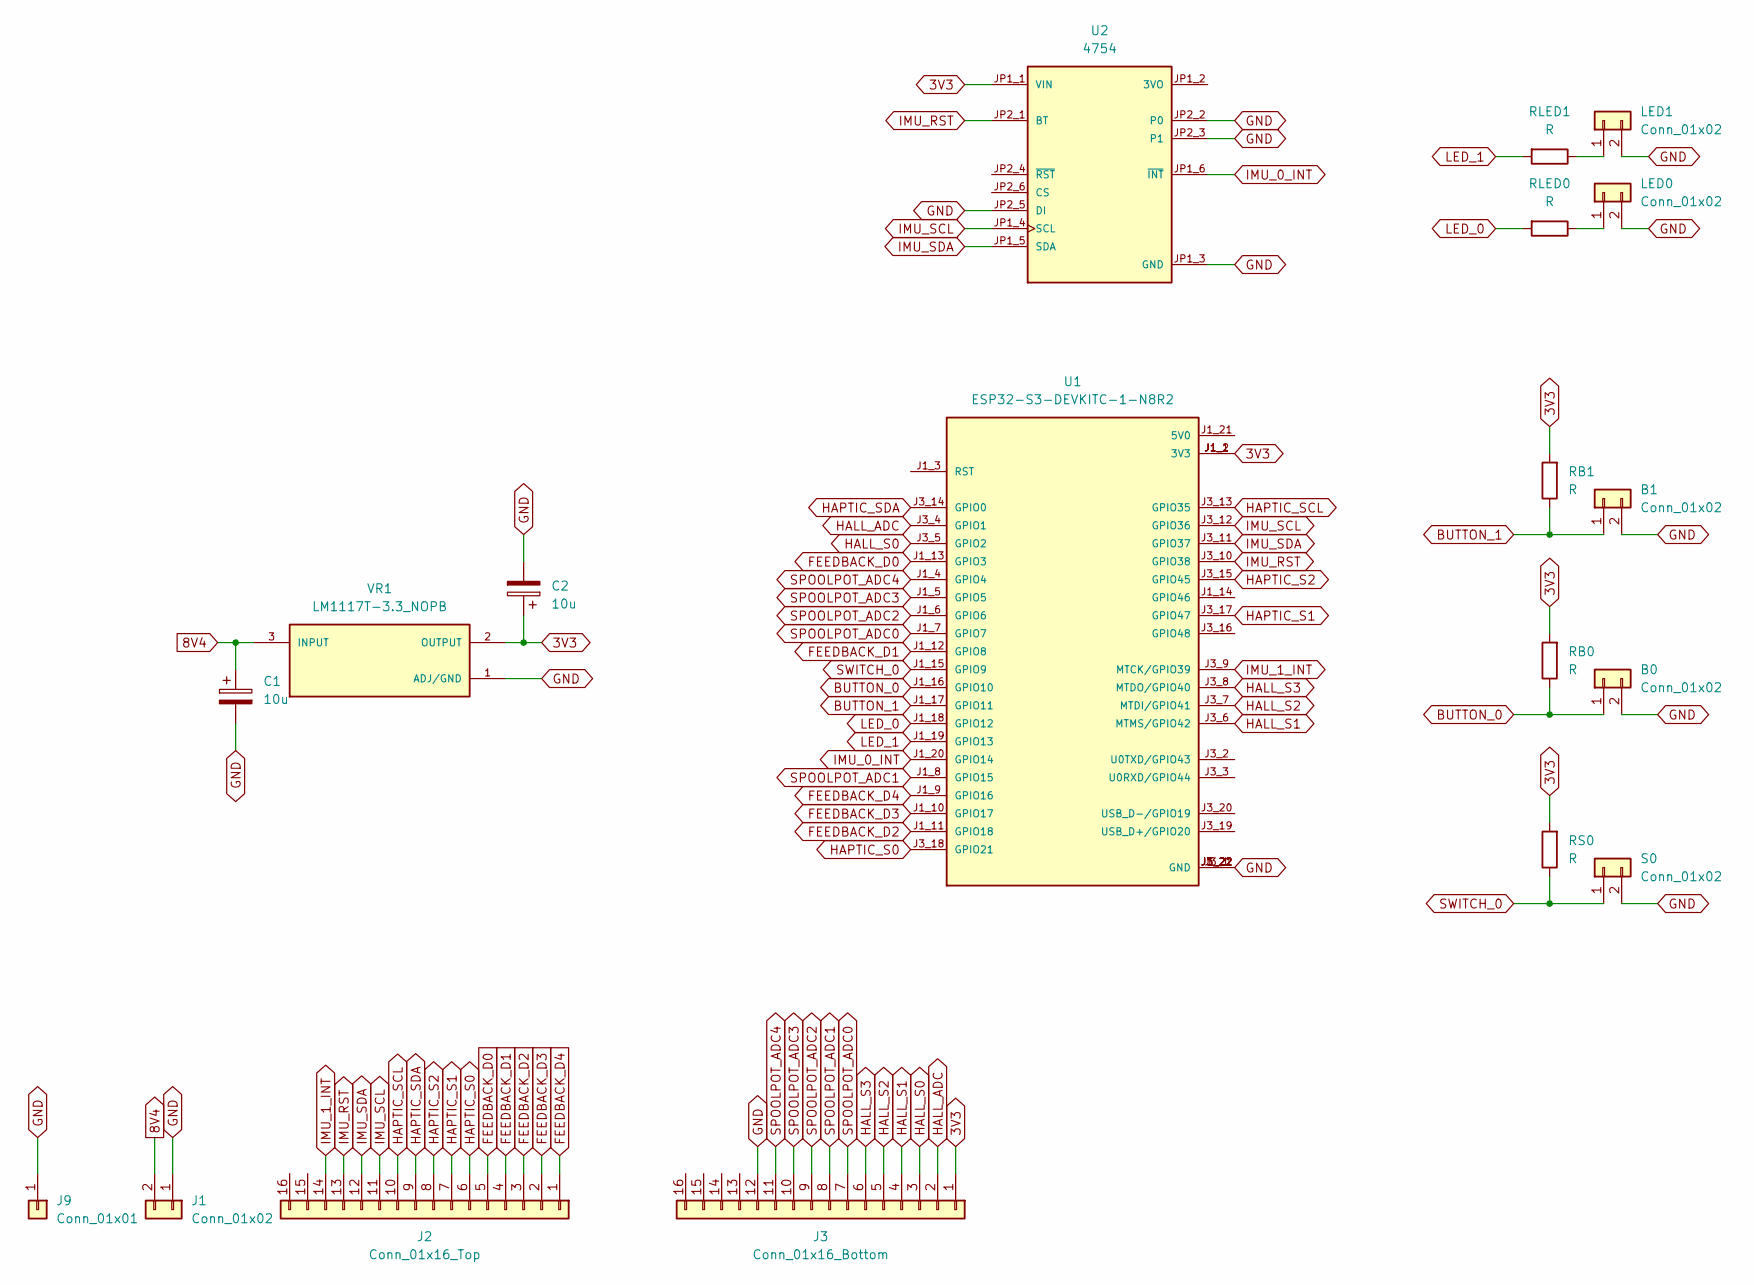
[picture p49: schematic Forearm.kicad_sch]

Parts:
B0, B1: Conn_01x02; PinSocket_1x02_P2.54mm_Vertical
C1, C2: 10u; C_1206_3216Metric
J1: Conn_01x02; PinSocket_1x02_P2.54mm_Vertical
J2: Conn_01x16_Top; CON_522071633_MOL
J3: Conn_01x16_Bottom; CON_522071633_MOL
J9: Conn_01x01; PinSocket_1x01_P2.54mm_Vertical
LED0, LED1: Conn_01x02; PinSocket_1x02_P2.54mm_Vertical
RB0, RB1: R; R_0402_1005Metric
RLED0, RLED1: R; R_0402_1005Metric
RS0: R; R_0402_1005Metric
S0: Conn_01x02; PinSocket_1x02_P2.54mm_Vertical
U1: ESP32-S3-DEVKITC-1-N8R2; XCVR_ESP32-S3-DEVKITC-1-N8R2; PARTREV V1
U2: 4754; MODULE_4754; PARTREV 2021-03-16
VR1: LM1117T-3.3_NOPB; PARTREV O

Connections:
3V3: C2.1, J3.1, RB0.2, RB1.2, RS0.2, U1.J1_1 (3V3), U1.J1_2 (3V3), U2.JP1_1 (VIN), VR1.2 (OUTPUT)
8V4: C1.1, J1.2, VR1.3 (INPUT)
BUTTON_0: B0.1, RB0.1, U1.J1_16 (GPIO10)
BUTTON_1: B1.1, RB1.1, U1.J1_17 (GPIO11)
FEEDBACK_D0: J2.5, U1.J1_13 (GPIO3)
FEEDBACK_D1: J2.4, U1.J1_12 (GPIO8)
FEEDBACK_D2: J2.3, U1.J1_11 (GPIO18)
FEEDBACK_D3: J2.2, U1.J1_10 (GPIO17)
FEEDBACK_D4: J2.1, U1.J1_9 (GPIO16)
GND: B0.2, B1.2, C1.2, C2.2, J1.1, J3.12, J9.1, LED0.2, LED1.2, S0.2, U1.J1_22 (GND), U1.J3_1 (GND), U1.J3_21 (GND), U1.J3_22 (GND), U2.JP1_3 (GND), U2.JP2_2 (P0), U2.JP2_3 (P1), U2.JP2_5 (DI), VR1.1 (ADJ/GND)
HALL_ADC: J3.2, U1.J3_4 (GPIO1)
HALL_S0: J3.3, U1.J3_5 (GPIO2)
HALL_S1: J3.4, U1.J3_6 (MTMS/GPIO42)
HALL_S2: J3.5, U1.J3_7 (MTDI/GPIO41)
HALL_S3: J3.6, U1.J3_8 (MTDO/GPIO40)
HAPTIC_S0: J2.6, U1.J3_18 (GPIO21)
HAPTIC_S1: J2.7, U1.J3_17 (GPIO47)
HAPTIC_S2: J2.8, U1.J3_15 (GPIO45)
HAPTIC_SCL: J2.10, U1.J3_13 (GPIO35)
HAPTIC_SDA: J2.9, U1.J3_14 (GPIO0)
IMU_0_INT: U1.J1_20 (GPIO14), U2.JP1_6 (~INT)
IMU_1_INT: J2.14, U1.J3_9 (MTCK/GPIO39)
IMU_RST: J2.13, U1.J3_10 (GPIO38), U2.JP2_1 (BT)
IMU_SCL: J2.11, U1.J3_12 (GPIO36), U2.JP1_4 (SCL)
IMU_SDA: J2.12, U1.J3_11 (GPIO37), U2.JP1_5 (SDA)
LED_0: RLED0.2, U1.J1_18 (GPIO12)
LED_1: RLED1.2, U1.J1_19 (GPIO13)
unnamed: LED0.1, RLED0.1
unnamed: LED1.1, RLED1.1
SPOOLPOT_ADC0: J3.7, U1.J1_7 (GPIO7)
SPOOLPOT_ADC1: J3.8, U1.J1_8 (GPIO15)
SPOOLPOT_ADC2: J3.9, U1.J1_6 (GPIO6)
SPOOLPOT_ADC3: J3.10, U1.J1_5 (GPIO5)
SPOOLPOT_ADC4: J3.11, U1.J1_4 (GPIO4)
SWITCH_0: RS0.1, S0.1, U1.J1_15 (GPIO9)

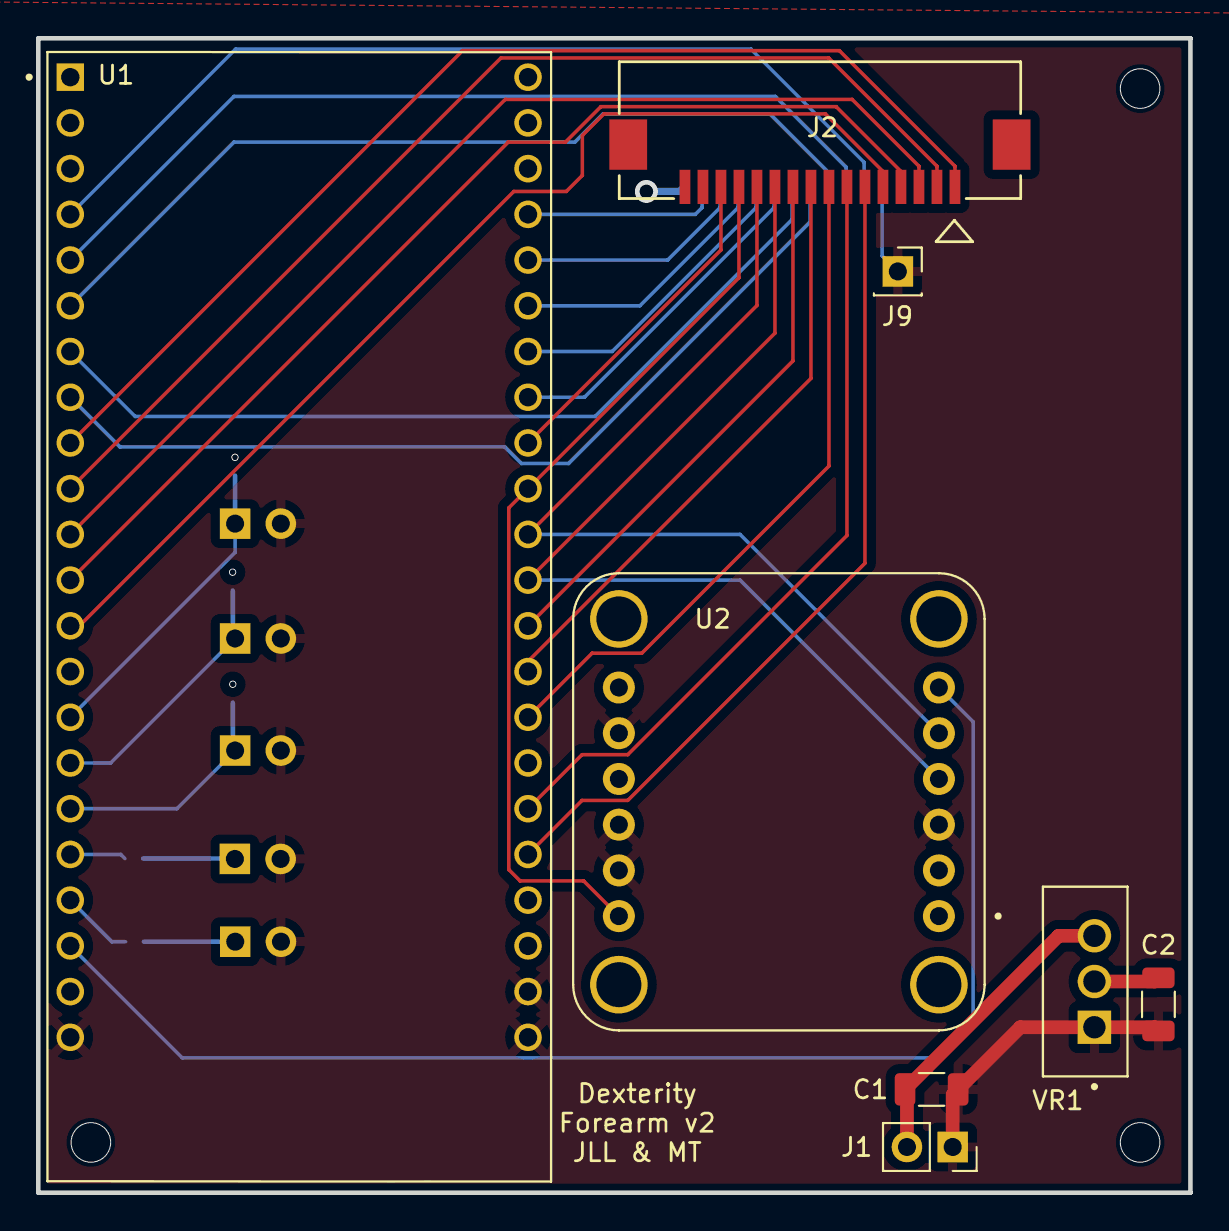
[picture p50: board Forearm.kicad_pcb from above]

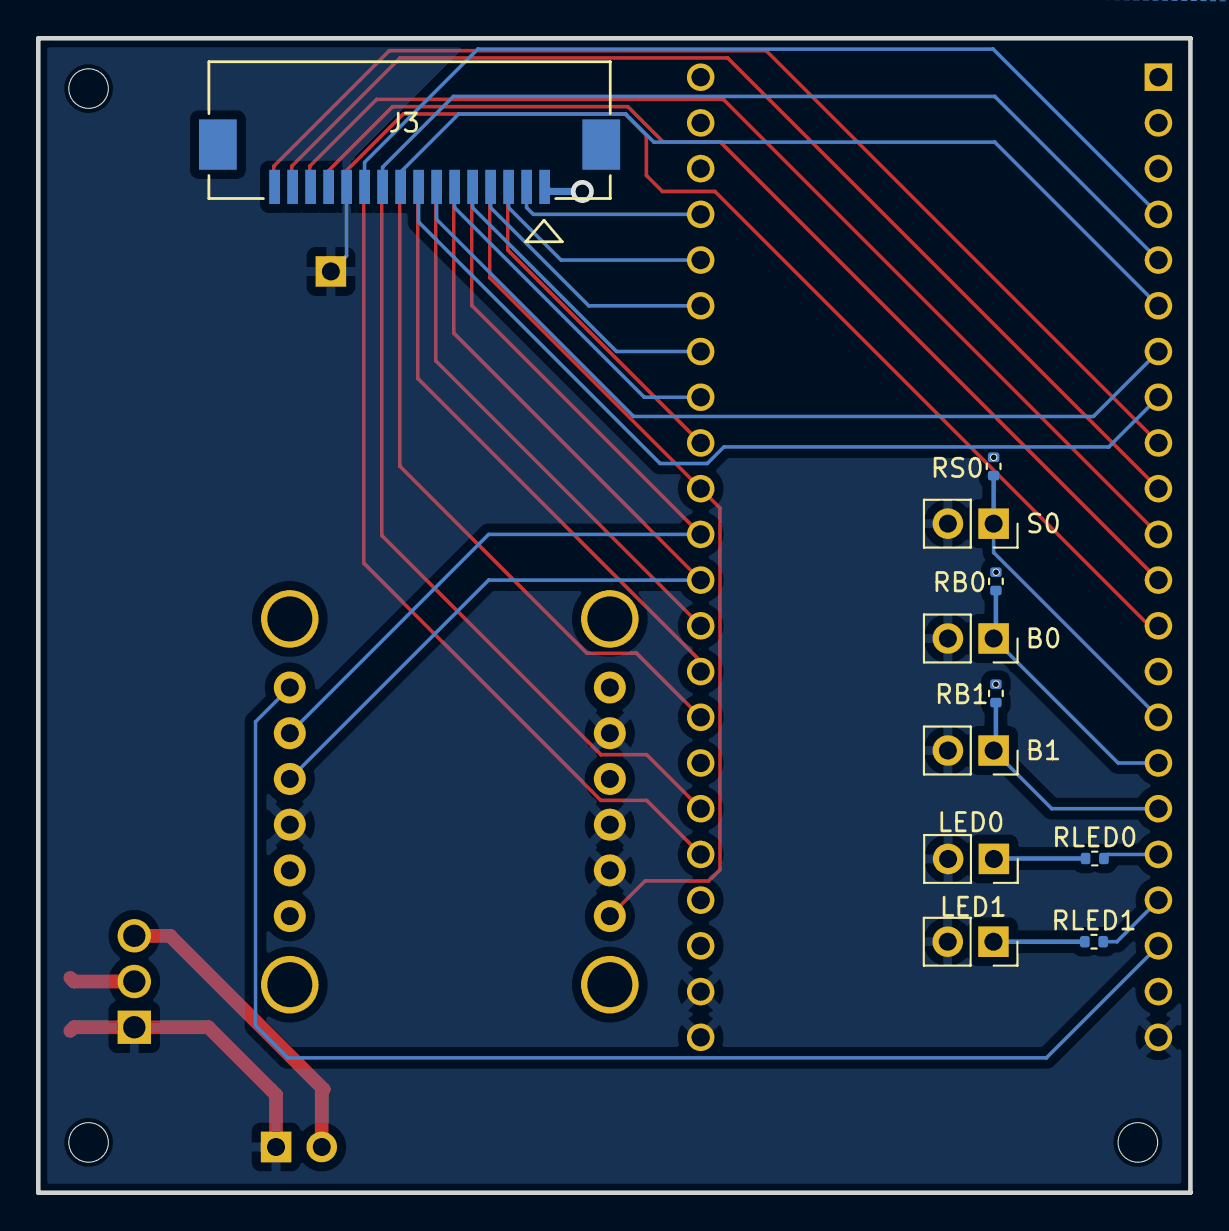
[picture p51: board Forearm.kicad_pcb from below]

Board: 4 copper layers, 64.0 x 64.1 mm, 19 parts (11 on the bottom side), 35 nets.

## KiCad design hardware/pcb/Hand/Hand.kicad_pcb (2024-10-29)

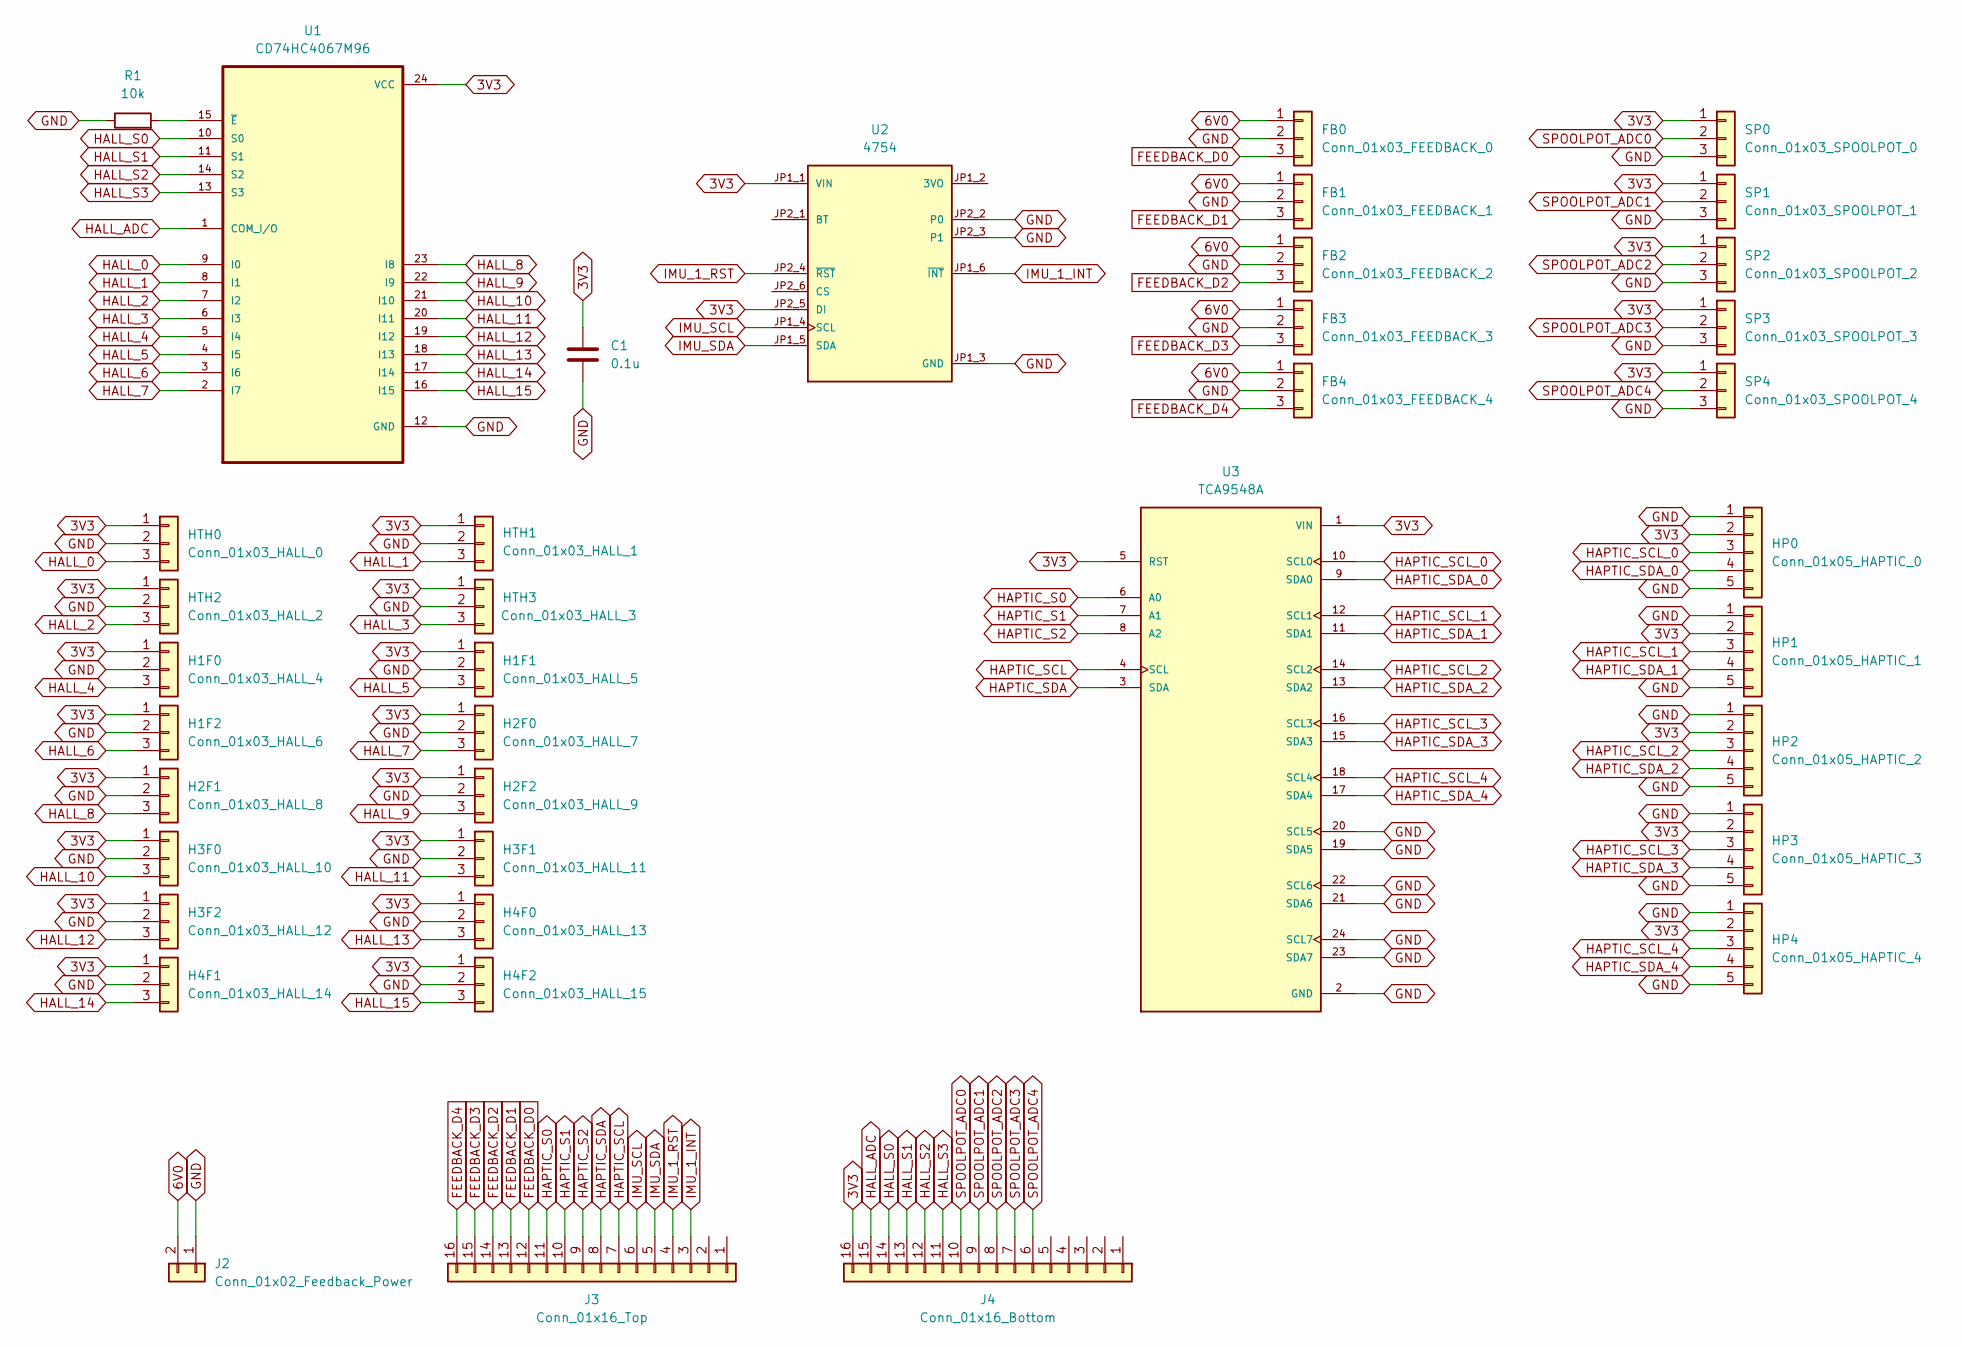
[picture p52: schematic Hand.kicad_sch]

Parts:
C1: 0.1u; C_1206_3216Metric
FB0: Conn_01x03_FEEDBACK_0; JST_SM03B-SRSS-TB_LF__SN_
FB1: Conn_01x03_FEEDBACK_1; JST_SM03B-SRSS-TB_LF__SN_
FB2: Conn_01x03_FEEDBACK_2; JST_SM03B-SRSS-TB_LF__SN_
FB3: Conn_01x03_FEEDBACK_3; JST_SM03B-SRSS-TB_LF__SN_
FB4: Conn_01x03_FEEDBACK_4; JST_SM03B-SRSS-TB_LF__SN_
H1F0: Conn_01x03_HALL_4; JST_SM03B-SRSS-TB_LF__SN_
H1F1: Conn_01x03_HALL_5; JST_SM03B-SRSS-TB_LF__SN_
H1F2: Conn_01x03_HALL_6; JST_SM03B-SRSS-TB_LF__SN_
H2F0: Conn_01x03_HALL_7; JST_SM03B-SRSS-TB_LF__SN_
H2F1: Conn_01x03_HALL_8; JST_SM03B-SRSS-TB_LF__SN_
H2F2: Conn_01x03_HALL_9; JST_SM03B-SRSS-TB_LF__SN_
H3F0: Conn_01x03_HALL_10; JST_SM03B-SRSS-TB_LF__SN_
H3F1: Conn_01x03_HALL_11; JST_SM03B-SRSS-TB_LF__SN_
H3F2: Conn_01x03_HALL_12; JST_SM03B-SRSS-TB_LF__SN_
H4F0: Conn_01x03_HALL_13; JST_SM03B-SRSS-TB_LF__SN_
H4F1: Conn_01x03_HALL_14; JST_SM03B-SRSS-TB_LF__SN_
H4F2: Conn_01x03_HALL_15; JST_SM03B-SRSS-TB_LF__SN_
HP0: Conn_01x05_HAPTIC_0; JST_SM05B-SRSS-TB_LF__SN_
HP1: Conn_01x05_HAPTIC_1; JST_SM05B-SRSS-TB_LF__SN_
HP2: Conn_01x05_HAPTIC_2; JST_SM05B-SRSS-TB_LF__SN_
HP3: Conn_01x05_HAPTIC_3; JST_SM05B-SRSS-TB_LF__SN_
HP4: Conn_01x05_HAPTIC_4; JST_SM05B-SRSS-TB_LF__SN_
HTH0: Conn_01x03_HALL_0; JST_SM03B-SRSS-TB_LF__SN_
HTH1: Conn_01x03_HALL_1; JST_SM03B-SRSS-TB_LF__SN_
HTH2: Conn_01x03_HALL_2; JST_SM03B-SRSS-TB_LF__SN_
HTH3: Conn_01x03_HALL_3; JST_SM03B-SRSS-TB_LF__SN_
J2: Conn_01x02_Feedback_Power; PinHeader_1x02_P2.54mm_Vertical
J3: Conn_01x16_Top; CON_522071633_MOL
J4: Conn_01x16_Bottom; CON_522071633_MOL
R1: 10k; R_0402_1005Metric
SP0: Conn_01x03_SPOOLPOT_0; JST_SM03B-SRSS-TB_LF__SN_
SP1: Conn_01x03_SPOOLPOT_1; JST_SM03B-SRSS-TB_LF__SN_
SP2: Conn_01x03_SPOOLPOT_2; JST_SM03B-SRSS-TB_LF__SN_
SP3: Conn_01x03_SPOOLPOT_3; JST_SM03B-SRSS-TB_LF__SN_
SP4: Conn_01x03_SPOOLPOT_4; JST_SM03B-SRSS-TB_LF__SN_
U1: CD74HC4067M96; SOIC127P1030X265-24N
U2: 4754; MODULE_4754; PARTREV 2021-03-16
U3: TCA9548A; MODULE_2717; PARTREV Sep 11, 2015

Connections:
3V3: C1.1, H1F0.1, H1F1.1, H1F2.1, H2F0.1, H2F1.1, H2F2.1, H3F0.1, H3F1.1, H3F2.1, H4F0.1, H4F1.1, H4F2.1, HP0.2, HP1.2, HP2.2, HP3.2, HP4.2, HTH0.1, HTH1.1, HTH2.1, HTH3.1, J4.16, SP0.1, SP1.1, SP2.1, SP3.1, SP4.1, U1.24 (VCC), U2.JP1_1 (VIN), U2.JP2_5 (DI), U3.1 (VIN), U3.5 (RST)
6V0: FB0.1, FB1.1, FB2.1, FB3.1, FB4.1, J2.2
FEEDBACK_D0: FB0.3, J3.12
FEEDBACK_D1: FB1.3, J3.13
FEEDBACK_D2: FB2.3, J3.14
FEEDBACK_D3: FB3.3, J3.15
FEEDBACK_D4: FB4.3, J3.16
GND: C1.2, FB0.2, FB1.2, FB2.2, FB3.2, FB4.2, H1F0.2, H1F1.2, H1F2.2, H2F0.2, H2F1.2, H2F2.2, H3F0.2, H3F1.2, H3F2.2, H4F0.2, H4F1.2, H4F2.2, HP0.1, HP0.5, HP1.1, HP1.5, HP2.1, HP2.5, HP3.1, HP3.5, HP4.1, HP4.5, HTH0.2, HTH1.2, HTH2.2, HTH3.2, J2.1, R1.1, SP0.3, SP1.3, SP2.3, SP3.3, SP4.3, U1.12 (GND), U2.JP1_3 (GND), U2.JP2_2 (P0), U2.JP2_3 (P1), U3.2 (GND), U3.19 (SDA5), U3.20 (SCL5), U3.21 (SDA6), U3.22 (SCL6), U3.23 (SDA7), U3.24 (SCL7)
HALL_0: HTH0.3, U1.9 (I0)
HALL_1: HTH1.3, U1.8 (I1)
HALL_2: HTH2.3, U1.7 (I2)
HALL_3: HTH3.3, U1.6 (I3)
HALL_4: H1F0.3, U1.5 (I4)
HALL_5: H1F1.3, U1.4 (I5)
HALL_6: H1F2.3, U1.3 (I6)
HALL_7: H2F0.3, U1.2 (I7)
HALL_8: H2F1.3, U1.23 (I8)
HALL_9: H2F2.3, U1.22 (I9)
HALL_10: H3F0.3, U1.21 (I10)
HALL_11: H3F1.3, U1.20 (I11)
HALL_12: H3F2.3, U1.19 (I12)
HALL_13: H4F0.3, U1.18 (I13)
HALL_14: H4F1.3, U1.17 (I14)
HALL_15: H4F2.3, U1.16 (I15)
HALL_ADC: J4.15, U1.1 (COM_I/O)
HALL_S0: J4.14, U1.10 (S0)
HALL_S1: J4.13, U1.11 (S1)
HALL_S2: J4.12, U1.14 (S2)
HALL_S3: J4.11, U1.13 (S3)
HAPTIC_S0: J3.11, U3.6 (A0)
HAPTIC_S1: J3.10, U3.7 (A1)
HAPTIC_S2: J3.9, U3.8 (A2)
HAPTIC_SCL: J3.7, U3.4 (SCL)
HAPTIC_SCL_0: HP0.3, U3.10 (SCL0)
HAPTIC_SCL_1: HP1.3, U3.12 (SCL1)
HAPTIC_SCL_2: HP2.3, U3.14 (SCL2)
HAPTIC_SCL_3: HP3.3, U3.16 (SCL3)
HAPTIC_SCL_4: HP4.3, U3.18 (SCL4)
HAPTIC_SDA: J3.8, U3.3 (SDA)
HAPTIC_SDA_0: HP0.4, U3.9 (SDA0)
HAPTIC_SDA_1: HP1.4, U3.11 (SDA1)
HAPTIC_SDA_2: HP2.4, U3.13 (SDA2)
HAPTIC_SDA_3: HP3.4, U3.15 (SDA3)
HAPTIC_SDA_4: HP4.4, U3.17 (SDA4)
IMU_1_INT: J3.3, U2.JP1_6 (~INT)
IMU_1_RST: J3.4, U2.JP2_4 (~RST)
IMU_SCL: J3.6, U2.JP1_4 (SCL)
IMU_SDA: J3.5, U2.JP1_5 (SDA)
unnamed: R1.2, U1.15 (~E)
SPOOLPOT_ADC0: J4.10, SP0.2
SPOOLPOT_ADC1: J4.9, SP1.2
SPOOLPOT_ADC2: J4.8, SP2.2
SPOOLPOT_ADC3: J4.7, SP3.2
SPOOLPOT_ADC4: J4.6, SP4.2

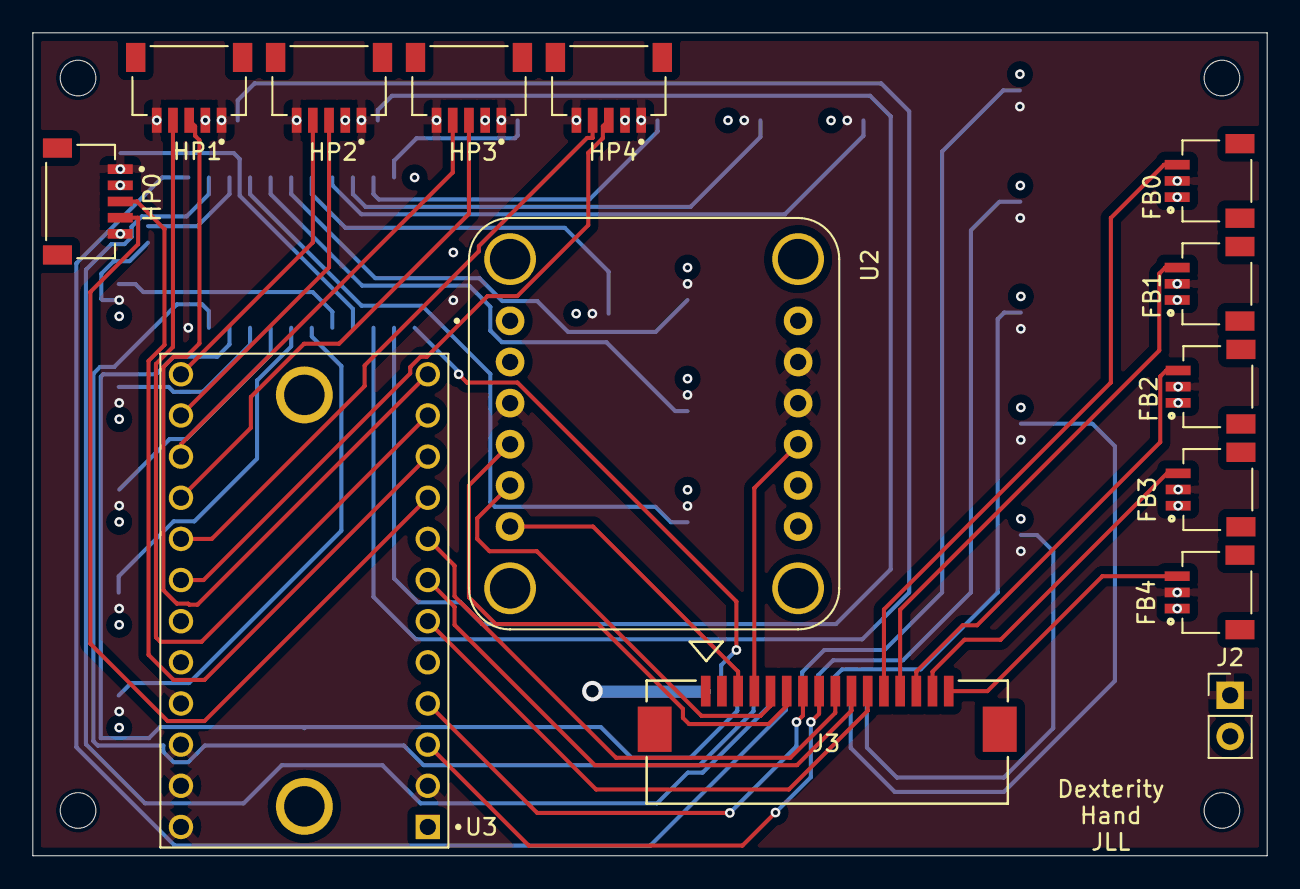
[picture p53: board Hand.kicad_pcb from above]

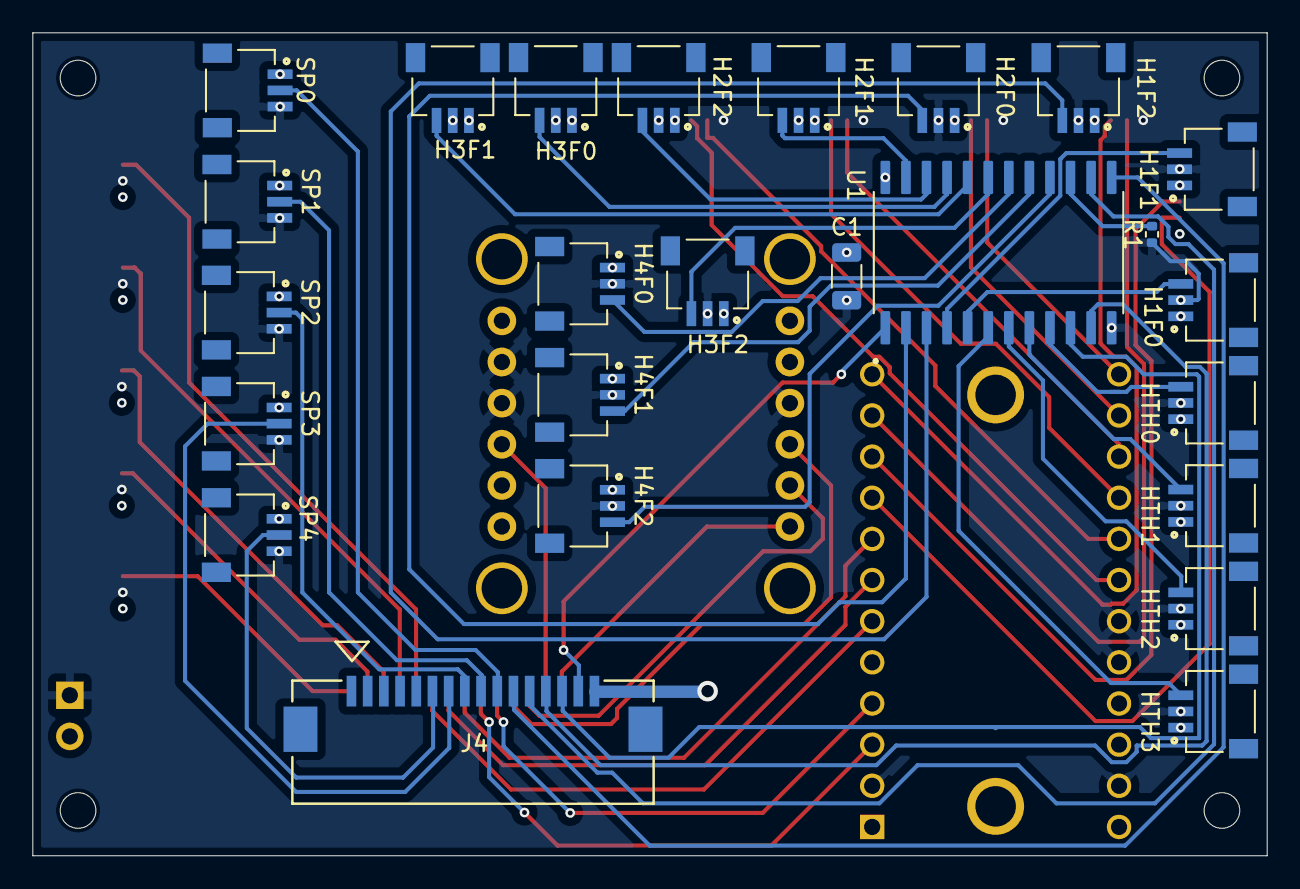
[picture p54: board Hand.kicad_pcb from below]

Board: 4 copper layers, 76.2 x 50.8 mm, 39 parts (25 on the bottom side), 54 nets.

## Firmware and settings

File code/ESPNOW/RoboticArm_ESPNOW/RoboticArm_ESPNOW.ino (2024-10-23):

#include <esp_now.h>
#include <WiFi.h>
#include <stdint.h>

// General_ESPNOW.h: 

#define ESPNOW_WIFI_CHANNEL 5            // WiFi channel to be used by ESP-NOW. The available channels will depend on your region.
#define ESPNOW_WIFI_MODE    WIFI_STA     // WiFi mode to be used by ESP-NOW. Any mode can be used.
#define ESPNOW_WIFI_IF      WIFI_IF_STA  // WiFi interface to be used by ESP-NOW. Any interface can be used.
#define DATA_RATE           100          // In Hz
#define SYNC_DELAY          10           // delay (in sec) between setting up ESPNOW and sending packets
#define PEER_MAC_1          {0x3C, 0x84, 0x27, 0x14, 0x7B, 0xB0} // MAC for board 1
#define PEER_MAC_2          {0x3C, 0x84, 0x27, 0xE1, 0xB3, 0x8C} // MAC for board 2

// Define the data packets
typedef struct position_packet {
  // remove when not monitoring success rate:
  int messages_rec;
  // end remove
  uint8_t finger_pos[16];
  uint8_t wrist_pos[3];
  uint8_t arm_pos[3];
} position_packet;

typedef struct haptic_packet {
  // remove when not monitoring success rate:
  int messages_rec;
  // end remove
  uint8_t force_index;
  uint8_t force_middle;
  uint8_t force_ring;
  uint8_t force_pinky;
  uint8_t force_thumb;
} haptic_packet;

// End General_ESPNOW.h

// Start RoboticArm_ESPNOW.h:

// Create an instance of the struct to be sent/received
// Create it in public space so general arm code can access values
position_packet arm_inData;
haptic_packet arm_outData;

// remove when not monitoring success rate:
int arm_messages_send_attempt;
int arm_messages_send_success;
int arm_messages_rcv;

// general arm code needs to initialize ESPNOW
void arm_ESPNOWsetup(uint8_t board_num);

// general arm code has access to sendData function
void arm_sendData(uint8_t fi, uint8_t fm, uint8_t fr, uint8_t fp, uint8_t ft);

// receive data function will call general arm code

void arm_monitorSuccess();

// End RoboticArm_ESPNOW.h

// Start RoboticArm_ESPNOW.c:

uint8_t peer_mac[6];

// remove when not monitoring success rate:
uint8_t pos5_in;
int sizeIn;
// end remove

// Function to handle the result of data send
void ArmOnDataSent(const uint8_t *mac_addr, esp_now_send_status_t status) {
  // Serial.print("\r\nLast Packet Send Status:\t");
  // Serial.println(status == ESP_NOW_SEND_SUCCESS ? "Delivery Success" : "Delivery Fail");
}

// Callback function that will be executed when data is received
void ArmOnDataRecv(const esp_now_recv_info *info, const uint8_t *incomingData, int len) {
  if (len == sizeof(arm_inData)) {
      memcpy(&arm_inData, incomingData, sizeof(arm_inData));
      // Proceed with processing
  } else {
      Serial.println("Received data length does not match expected size.");
  }
  // Serial.print("Bytes received: ");
  // Serial.println(len);
  // Serial.print("Message: ");
  // Serial.println(inData.str);
  // Serial.print("finger_position_1: ");
  // Serial.println(inData.finger_position_1);
  // Serial.print("finger_angle_1: ");
  // Serial.println(inData.finger_angle_1);
  // Serial.print("wrist_position: ");
  // Serial.println(inData.wrist_position);
  // Serial.print("wrist_angle: ");
  // Serial.println(inData.wrist_angle);
  // Serial.println();
  arm_messages_send_success = arm_inData.messages_rec;
  arm_messages_rcv++;
  pos5_in = arm_inData.finger_pos[5];
  sizeIn = len;
}

void arm_ESPNOWsetup(uint8_t board_num){
  arm_messages_send_attempt = 0;
  arm_messages_send_success = 0;
  arm_messages_rcv = 0;

  switch(board_num){
    case(1): {
      uint8_t temp[] = PEER_MAC_1;
      for(int j=0; j<6; j++){
        peer_mac[j] = temp[j];
      }
      break;
    }
    case(2): {
      uint8_t temp[] = PEER_MAC_2;
      for(int j=0; j<6; j++){
        peer_mac[j] = temp[j];
      }
      break;
    }
    deafult:
      Serial.print("ERROR: Board num not recognized in arm_ESPNOWsetup. Board received: ");
      Serial.println(board_num);
      while(1) delay(10000);
  }

  while (!Serial) {
    delay(10);
  }

  // Set the WiFi to the mode and channel to be used by ESP-NOW
  Serial.println("Setting up WiFi...");
  WiFi.mode(ESPNOW_WIFI_MODE);
  WiFi.setChannel(ESPNOW_WIFI_CHANNEL, WIFI_SECOND_CHAN_NONE);

  // Wait for the WiFi to start
  while (!WiFi.STA.started()) {
    delay(100);
  }

  // Print the MAC address of this device
  Serial.print("MAC Address: ");
  Serial.println(WiFi.macAddress());

  // Initialize ESP-NOW
  if (esp_now_init() != ESP_OK) {
    Serial.println("Error initializing ESP-NOW");
    return;
  }

  // Register the send callback function
  esp_now_register_send_cb(ArmOnDataSent);

  // Register the receive callback function
  esp_now_register_recv_cb(ArmOnDataRecv);

  // Add the peer (receiver) device
  esp_now_peer_info_t peerInfo;
  memset(&peerInfo, 0, sizeof(peerInfo));  // Clear the peer info
  memcpy(peerInfo.peer_addr, peer_mac, 6); // Set peer MAC address
  peerInfo.channel = ESPNOW_WIFI_CHANNEL;  // Same WiFi channel as sender
  peerInfo.encrypt = false;  // No encryption
  
  if (esp_now_add_peer(&peerInfo) != ESP_OK) {
    Serial.println("Failed to add peer");
    return;
  }

  // DELAY: enter delay if trying to sync up MAC addresses
  delay(SYNC_DELAY*1000);
}

void arm_sendData(uint8_t fi, uint8_t fm, uint8_t fr, uint8_t fp, uint8_t ft){
  // Set values to send
  arm_outData.force_index = fi;
  arm_outData.force_middle = fm;
  arm_outData.force_ring = fr;
  arm_outData.force_pinky = fp;
  arm_outData.force_thumb = ft;
  arm_outData.messages_rec = arm_messages_rcv;

  // Send struct message via ESP-NOW
  esp_err_t result = esp_now_send(peer_mac, (uint8_t *)&arm_outData, sizeof(arm_outData));

  arm_messages_send_attempt += 1;

  if (result == ESP_OK) {
    // Serial.println("Sent with success");
  } else {
    Serial.println("Error sending the data");
  }
}

void arm_monitorSuccess(){
  Serial.println();
  Serial.print("Messages Sent: ");
  Serial.println(arm_messages_send_attempt);
  Serial.print("Messages Delivered: ");
  Serial.println(arm_messages_send_success);
  Serial.print("Success rate: ");
  Serial.print(arm_messages_send_success*100/arm_messages_send_attempt);
  Serial.println(" %");
  Serial.print("position 5: ");
  Serial.println(pos5_in);
  Serial.print("size in: ");
  Serial.println(sizeIn);
  Serial.println();
}

// End RoboticArm_ESPNOW.c

// General Arduino Code for Demonstration

int i;

void setup() {
  // Start the Serial Monitor
  Serial.begin(115200);
  arm_ESPNOWsetup(2);
  i = 0;
}

void loop() {

  // arm_sendData(random(1, 100), random(1, 100), random(1, 100), random(1, 100), random(1, 100));

  // delay(1000/DATA_RATE);  // Wait before sending again


  // i += 1;
  // if(i % 200 == 0){
  //   arm_monitorSuccess();
  // }
}

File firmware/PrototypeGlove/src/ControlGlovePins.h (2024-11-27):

// file to define pins on ESP32 board

// left side pins
#define SPOOL_POT_ADC0 4        // 4
#define SPOOL_POT_ADC1 5        // 5
#define SPOOL_POT_ADC2 6        // 6
#define SPOOL_POT_ADC3 7        // 7
#define SPOOL_POT_ADC4 15       // 15
#define FEEDBACK_SERVO_D4 16    // 16
#define FEEDBACK_SERVO_D3 17    // 17
#define FEEDBACK_SERVO_D2 18    // 18
#define FEEDBACK_SERVO_D1 8     // 8
#define FEEDBACK_SERVO_D0 3     // 3
// pin 46 unused                // 46
#define SWITCH_0 9              // 9
#define BUTTON_0 10             // 10
#define BUTTON_1 11             // 11
#define LED_0 12                // 12
#define LED_1 13                // 13
#define IMU_INT_0 14            // 14

// right side pins
#define U0_TX 43                // TX
#define U0_RX 44                // RX
#define HALL_ADC 1              // 1
#define HALL_S0 2               // 2
#define HALL_S1 42              // 42
#define HALL_S2 41              // 41
#define HALL_S3 40              // 40
#define IMU_INT_1 39            // 39
#define IMU_RST 38              // 38
#define IMU_SDA 37              // 37
#define IMU_SCL 36              // 36
#define HAPTIC_SCL 35           // 35
#define HAPTIC_SDA 0            // 0
#define HAPTIC_S2 45            // 45
#define INTERNAL_RGB_LED 48     // 48
#define HAPTIC_S1 47            // 47
#define HAPTIC_S0 21            // 21
#define USB_D_PLUS 20           // 20
#define USB_D_MINUS 19          // 19

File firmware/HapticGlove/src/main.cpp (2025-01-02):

#include <HapticGlove_ESPNOW.h>
#include <HapticGlove.h>
#include "GloveControl.h"
#include "HapticFeedback.h"
#include "IMU.hpp"
#include "GloveControl.h"
#include <Adafruit_I2CDevice.h>
#include <SPI.h>
#include "driver/gpio.h"
// General Arduino Code for Demonstration

TaskHandle_t sensorProcessing;
TaskHandle_t hapticControl;

volatile bool ESPNOW_setup;

gpio_config_t myGPIOconfig;

hw_timer_t *Timer0 = NULL;
volatile bool timer0_triggered = false; // Flag to indicate timer interrupt occurrence
hw_timer_t *Timer1 = NULL;
volatile bool timer1_triggered = false; // Flag to indicate timer interrupt occurrence

void IRAM_ATTR Timer0_ISR();
void IRAM_ATTR Timer1_ISR();
void IRAM_ATTR button_0_isr();
void IRAM_ATTR button_1_isr();

uint8_t button_counter;

GloveControlPanel controlPanel = GloveControlPanel(&button_0_isr, &button_1_isr);
volatile bool button_pressed = false;

void triggerGloveControl(){
  sendPositionData();
}

void triggerHapticFeedback(){
  triggerFeedback();
}

void hapticControlCode(void* params){
  Serial.print("Setting up hapticControl from core ");
  Serial.println(xPortGetCoreID());
  setupFeedback();
  uint8_t mac[] = PEER_MAC;
  glove_ESPNOWsetup(mac);
  ESPNOW_setup = true;

  Timer0 = timerBegin(0, 80, true); // timer speed (Hz) = Timer clock speed (Mhz) / prescaler --> 1 MHz
  timerAttachInterrupt(Timer0, &Timer0_ISR, true); // Attach ISR to Timer0
  timerAlarmWrite(Timer0, 1000000/ISR0_FREQ, true); // Set timer to trigger every 1,000,000/ISR0_FREQ microseconds (1 s/f)
  timerAlarmEnable(Timer0); // Enable the timer alarm

  while (1) {
      if (timer0_triggered) { 
          timer0_triggered = false; // Reset the flag
          triggerHapticFeedback();
      }
      if (button_pressed){
        button_counter--;
        setupFeedback();
        if(button_counter == 0){
          button_pressed = false;
        }
      }
      vTaskDelay(10 / portTICK_PERIOD_MS); // Yield CPU for 10 ms to prevent blocking other tasks
  }

}

void sensorProcessingCode(void* params){
  gloveControlSetup();
  while(!ESPNOW_setup){
    vTaskDelay(10 / portTICK_PERIOD_MS); // Yield CPU for 20 ms
  }
  Serial.print("Setting up sensorProcessing from core ");
  Serial.println(xPortGetCoreID());

  Timer1 = timerBegin(1, 80, true); // timer speed (Hz) = Timer clock speed (Mhz) / prescaler --> 1 MHz
  timerAttachInterrupt(Timer1, &Timer1_ISR, true); // Attach ISR to Timer1
  timerAlarmWrite(Timer1, 1000000/ISR1_FREQ, true); // Set timer to trigger every 1,000,000/ISR1_FREQ microseconds (1 s/f)
  timerAlarmEnable(Timer1); // Enable the timer alarm

  while (1) {
      if (timer1_triggered) { 
          timer1_triggered = false; // Reset the flag
          triggerGloveControl();
      }
      if (button_pressed){
        button_counter--;
        // if(IMUS_CONNECTED){
        //   initializeIMUs();
        //   calibrateIMUs();
        // }
        fingerTrackingSetup();
        if(button_counter == 0){
          button_pressed = false;
        }
      }
      vTaskDelay(10 / portTICK_PERIOD_MS); // Yield CPU for 10 ms to prevent blocking other tasks
  }
}

void IRAM_ATTR button_0_isr(){
  return;
}

void IRAM_ATTR button_1_isr(){
  button_pressed = true;
  button_counter = 2;
}

void setup() {
  myGPIOconfig.pin_bit_mask = (0x1);
  myGPIOconfig.pull_down_en = GPIO_PULLDOWN_DISABLE;
  myGPIOconfig.pull_up_en = GPIO_PULLUP_DISABLE;
  myGPIOconfig.mode = GPIO_MODE_OUTPUT;
  myGPIOconfig.intr_type = GPIO_INTR_DISABLE;
  gpio_config(&myGPIOconfig);
  button_counter = 0;
  // Start the Serial Monitor
  int baud_rate = 115200;
  Serial.begin(baud_rate);
  Serial.println("initializing . . .");
  controlPanel.initialize();
  controlPanel.setIntLED(1);
  controlPanel.setIntLEDColor(0, 0, 255); //blue
  delay(1000);
  ESPNOW_setup = false;
  button_pressed = false;
  Serial.println("Control Panel");
  Serial.println("IMUs");
  // IMU initialization and calibration
  if(IMUS_CONNECTED){
    controlPanel.setIntLED(1);
    controlPanel.setIntLEDColor(255, 0, 0); //red
    delay(1000);
    Serial.println("init IMUs");
    initializeIMUs();
    controlPanel.setIntLED(1);
    controlPanel.setIntLEDColor(193, 28, 132); // pink
    delay(1000);
    Serial.println("calibrate IMUs");
    calibrateIMUs(); // pink at wait nonzero and purple at wait button
    delay(1000);
  }
  controlPanel.setIntLED(1);
  controlPanel.setIntLEDColor(255, 102, 0); // orange
  delay(1000);
  fingerTrackingSetup();
  controlPanel.setIntLED(0);

      // assign armControl to core 0
    xTaskCreatePinnedToCore(
        hapticControlCode,   // function
        "hapticControl",     // name
        10000,       // stack depth
        NULL,        // parameters (void*)
        1,           // uxPriority
        &hapticControl,      // task handle (tracking)
        0);          // coreID

    // assign pressureSensor to core 1
    xTaskCreatePinnedToCore(
        sensorProcessingCode,   // function
        "sensorProcessing",     // name
        10000,       // stack depth
        NULL,        // parameters (void*)
        1,           // uxPriority
        &sensorProcessing,      // task handle (tracking)
        1);          // coreID
}

// Interrupt Service Routine (ISR) for Timer0
void IRAM_ATTR Timer0_ISR() {
  timer0_triggered = true;  // Set a flag for the task to handle instead of printing directly
}

// Interrupt Service Routine (ISR) for Timer1
void IRAM_ATTR Timer1_ISR() {
  timer1_triggered = true;  // Set a flag for the task to handle instead of printing directly
}

void loop() {}

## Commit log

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2024-10-03 moved imu coms arduino code to a folder
2024-10-09 rough first version of pcbs
2024-10-09 added symbol and footprint files
2024-10-10 draft schematic for MDR
2024-10-13 replaced KiCad project zip files w/ raw project files
    [Forearm.kicad_pcb, Forearm.kicad_sch, Hand.kicad_pcb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]
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2024-10-21 fixed arduino folders
2024-10-22 merging jackson pcb into main
    [Forearm.kicad_pcb, Forearm.kicad_sch, Hand.kicad_pcb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]
2024-10-22 re-routed forearm board w/o switches etc
    [Forearm.kicad_pcb, Forearm.kicad_sch]
2024-10-23 Update to represent correct finger pos vals
    [HapticGlove_ESPNOW.ino]
2024-10-23 revised pcbs in preparation for pcb review; added pull-ups etc to forearm
    [Forearm.kicad_pcb, Forearm.kicad_sch, Hand.kicad_pcb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]
2024-10-23 re-work of pcbs for pin issues in progress 1
    [Forearm.kicad_pcb, Forearm.kicad_sch]
2024-10-25 revised pcbs in prep for manufacture, rev2
    [Forearm.kicad_pcb, Forearm.kicad_sch, Hand.kicad_pcb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]
2024-10-25 pcbs for order, rev3
    [Forearm.kicad_pcb]
2024-10-25 hand boatd final?
    [Hand.kicad_pcb]
2024-10-25 actually final pcbs
    [Forearm.kicad_pcb]
2024-10-25 updated symbols & footprints
2024-10-25 added ground pours and generated gerbers for pcbs
    [Forearm.kicad_pcb, Hand.kicad_pcb]
2024-10-27 updated arduinio sketch to work with both servos
2024-10-27 added second servo to arduino sketch
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2024-10-28 one finger working with flexion and abduction of the MCP joint
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2024-10-31 moved prototype glove code to this repo and started working on calibration
2024-11-03 calibration working for mcp flexion and abduction in PrototypeGlove project
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2024-11-10 firstpass at re-factoring Hall effect sensor code into library
2024-11-10 polished Hall effect sensor library; added docstrings for public interface
2024-11-12 added library files and updated forearm schematic
    [Forearm.kicad_sch]
2024-11-12 edited esp32 footprint
    [Forearm.kicad_pcb]
2024-11-13 updated esp32 pins on schematic
    [Forearm.kicad_pcb, Forearm.kicad_sch]
2024-11-13 board done will upload to JCL to check for errors
    [Forearm.kicad_pcb, Forearm.kicad_sch]
2024-11-13 forearm ready to be manufactured
    [Forearm.kicad_pcb]
2024-11-13 created test project to see if hand PCB hall effect sensors work
2024-11-13 send PCB off to JLC and cleaned up folders
2024-11-14 tested orginal 8 motor functionatlity with the more complete hand
2024-11-17 found out that esp32s3 only has 8 pwn channels, gonna start working on using a separate 16 channel PWN board
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2024-11-20 fixed bug that caused tip movment to be controlled by mcp flexion
    [main.cpp]
2024-11-25 started itegrating hall effect lib by cleaning up syntax errors
    [HallEffectSensors.cpp, main.cpp]
2024-11-25 code running but not working
    [main.cpp]
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2024-11-25 working on separating hall effect sensor library into finger tracking library
2024-11-26 HallEffectSensor and FingerTracking library work with prototype glove
2024-11-26 libraries work but are noisier than Prototype Glove code for some reason...
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2024-11-26 made v1 of finger attachment mechanism
    [finger lower v1.SLDPRT, finger upper v1.SLDPRT]
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2024-11-26 updated haptic library; created driver for LRA/FSR test
2024-11-26 finger tracking lib is creating less noisy data now
2024-11-27 RoboticArm works with ESP32 swapped board
    [main.cpp]
2024-11-27 arm control lib working from the bottom up
2024-11-27 updated RoboticArm and HapticGlove projects. Fixed Guru Errors
    [main.cpp]
2024-11-27 cleaned up FingerTracking, EmaxServoControl, and ArmControl and added servo position printing
    [16_emax_servos.json]
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2024-11-30 created v2 of finger upper and lower
    [curved arm.SLDPRT, curved arm.STL, finger lower v2.SLDPRT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]
2024-11-30 edit updated angle measurement lines
    [finger upper v2.SLDPRT]
2024-11-30 almost done with arm and joint mechanism
    [Mirrorhall effect holder.SLDPRT, curved arm v1.SLDPRT, curved arm v2.SLDPRT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]
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2024-12-01 adjusted wrist pos data size in robotic arm
2024-12-01 v2.2 of control glove finger tracker
    [curved arm v21.SLDPRT, finger and arms.SLDASM, hall effect holder abduction.SLDPRT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]
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2024-12-01 added tentative support for i2c mux to HapticFeedback
2024-12-02 working on v2.4
    [Mirrorhall effect holder.SLDPRT, curved arm v1.SLDPRT, curved arm v2.SLDPRT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]
2024-12-03 added define to remove blocking if IMUs disconnected
2024-12-04 grounded a0-a2 pins of i2c mux in setupFeedback method
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2024-12-04 forearm enclosure
    [finger upper v4.SLDPRT, finger upper v4.STL, forearm enclosure bottom v4.SLDPRT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]
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2024-12-08 reverted to code from 12-2, integrated hall effect v2
    [main.cpp]
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2024-12-09 integration for glove control panel, pressure sensors in robotic arm
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2024-12-09 fixed error in hall effect filter
2024-12-10 changes during demo day to robotic arm and halleffectlibtest
2024-12-11 int LED: initialization -- blue -> controlPanel -> (ifIMU red -> initIMU -> pink -> checknonzero -> purple -> wait for button ->) orange -> finger tracking -> off . . . calibration green until done
2024-12-11 wifi data not sending to hand
    [noisy_combined_sine_data.csv, smoothed_data.csv, smoothed_data_causal.csv]
2024-12-11 resolved pressuresensors conflict
2024-12-26 reorganization of project and started working on readmes
    [smoothed_data.csv, smoothed_data_causal.csv]
2024-12-26 reorganizing CAD files
    [Mirrorhall effect holder.SLDPRT, Thumb joint.SLDASM, amp meter holder.SLDPRT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]
2024-12-26 further reorganizing cad files
    [curved arm v4.STL, finger lower v4.STL, finger upper v4.1.STL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]
2024-12-26 added forearm enclosure and thumb attachment stls
    [forearm enclosure bottom v4.STL, forearm enclosure middle v4.STL, thumb attachment v4.STL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]
2024-12-28 more organization
    [amp meter holder.STL, arm base v2.STL, dexhand shell zipper.SLDPRT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]
2024-12-29 restructure project and working on the main readme
    [16_emax_servos.json, Forearm.kicad_pcb, Forearm.kicad_sch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]
2025-02-11 Update Thumb joint.SLDASM
    [Thumb joint.SLDASM]
